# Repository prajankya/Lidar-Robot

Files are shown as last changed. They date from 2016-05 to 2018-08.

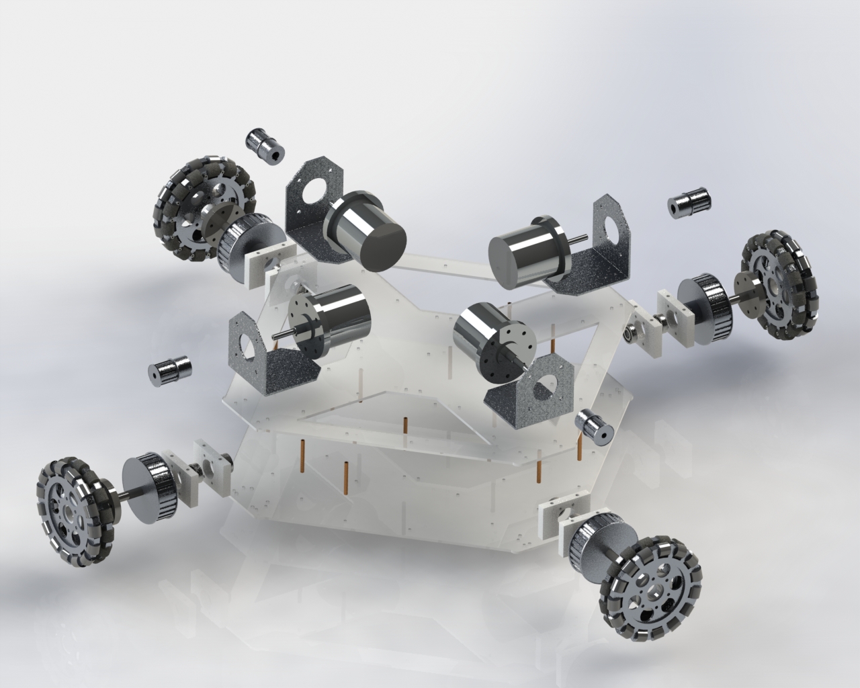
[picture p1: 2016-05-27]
Documentation/designs/r1.jpg

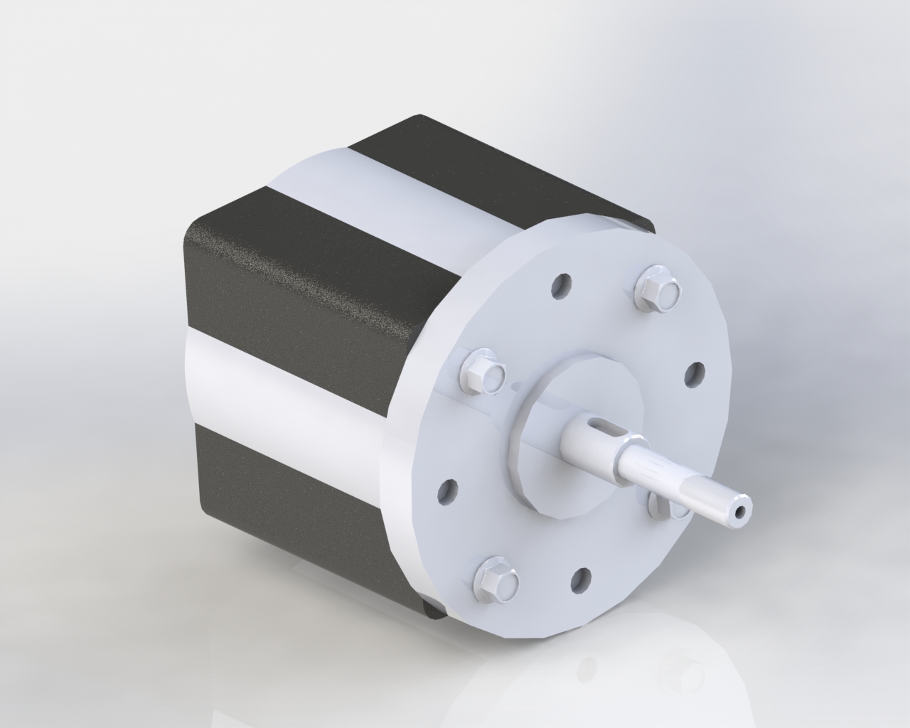
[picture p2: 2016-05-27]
Documentation/designs/r2.jpg

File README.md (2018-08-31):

  

## Unmanned Mapping Vehicle Using L.O.A.M. in Real-time
 L.O.A.M. - Lidar Odometry and Mapping in Real-time

This project is about an Unmanned Mobile Robot using L.O.A.M. (Lidar, Odometry And Mapping) in Real-time.

## Abstract
The robot uses a Laser distance sensor(Lidar) which gives distance to the first obstacle in its line-of-sight and the sensor. Making this sensor rotate gives us distance of all the obstacles from the sensor, which in fact is the map of the surrounding. This sensor, with other sensors like odometry and IMU(Inertial measurement Unit), mounted on a mobile moving base and complex algorithms driving the robot autonomously help make a to-scale map of the surrounding.

## Basic contruction
The Bot uses ROS(Robot Operating System) at its core running on a compact mobile CPU. It uses IMU(Inertial measurement Unit) for its orientation feedback. The base comprise of a square frame with four omni wheel on its corners driven by high torque BLDC motors. The Bot works on 24v DC and have internal power distribution and conversion unit. The bot first takes in the lidar input, and process that into a map fusing together with  odometry input and IMU input. The Odometry sensor is a “Castor Feedback sensor” which consist of two rotary encoders, one reading the angle or rotation, and other the length in that direction. This type of feedback can be universally used for any type of terrain robots with very good accuracy. This bot can be controlled from a remote computer, on which we can even see the 3D Model and see the model within the map in Real time. The GUI remote can be used to save the map or load the map in the system. Taking all the properties in consideration,  Lidar Robot with L.O.A.M. is a very robust platform with variety of robotics applications.

## How to Install
rosdep install --from-paths /opt/ros/jade --ignore-src

rosdep install --from-paths Lidar-Robot/src --ignore-src

6th sem, 2017 Batch  
Department of Automation and Robotics.  
B. V. Bhoomaraddi College of Engineering and Technology, Hubli  









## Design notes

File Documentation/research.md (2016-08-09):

#Papers which are to be refered

###Mapping with Synthetic 2D LIDAR in 3D Urban Environment
>Z. J. Chong, B. Qin, T. Bandyopadhyay, M. H. Ang, E. Frazzoli, and D. Rus, “Mapping with synthetic 2D LIDAR in 3D urban environment,” in 2013 IEEE/RSJ International Conference on Intelligent Robots and Systems, 2013, pp. 4715–4720.

In this paper, we report a fully automated detailed
mapping of a challenging urban environment using single
LIDAR. To improve scan matching, extended correlative scan
matcher is proposed. Also, a Monte Carlo loop closure detec-
tion is implemented to perform place recognition efficiently.
Automatic recovery of the pose graph map in the presence of
false place recognition is realized through a heuristic based
loop closure rejection. This mapping framework is evaluated
through experiments on the real world dataset obtained from
NUS campus environment.

###2D LIDAR Aided INS for vehicle positioning in urban environments
>S. Zhao and J. A. Farrell, “2D LIDAR Aided INS for vehicle positioning in urban environments,” in 2013 IEEE International Conference on Control Applications (CCA), 2013, pp. 376–381.

This paper presents a novel method to utilize 2D LIDAR for INS (Inertial Navigation System) aiding to improve 3D vehicle position estimation accuracy, especially when GNSS signals are shadowed. In the proposed framework, 2D LIDAR aiding is carried out without imposing any assumptions on the vehicle motion (e.g. we allow full six degree-of freedom motion). To achieve this, a closed-form formula is derived to predict the line measurement in the LIDAR's frame. This makes the feature association, residual formation and GUI display possible. With this formula, the Extended Kalman Filter (EKF) can be employed in a straightforward manner to fuse the LIDAR and IMU data to estimate the full state of the vehicle. Preliminary experimental results show the effectiveness of the LIDAR aiding in reducing the state estimation uncertainty along certain directions, when GNSS signals are shadowed.

#Literature Reviews to be refered

###A Review and Analysis of Literature on Autonomous Driving
>by Juan Rosenzweig, Michael Bartl

###An Evaluation of 2D SLAM Techniques Available in Robot Operating System
>J. M. Santos, D. Portugal, and R. P. Rocha, “An evaluation of 2D SLAM techniques available in robot operating system,” in 2013 IEEE International Symposium on Safety, Security, and Rescue Robotics (SSRR), 2013, pp. 1–6.

In this work, a study of several laser-based 2D
Simultaneous Localization and Mapping (SLAM) techniques
available in Robot Operating System (ROS) is conducted. All
the approaches have been evaluated and compared in 2D
simulations and real world experiments. In order to draw
conclusions on the performance of the tested techniques, the
experimental results were collected under the same conditions
and a generalized performance metric based on the k-nearest
neighbors concept was applied. Moreover, the CPU load of each
technique is examined.
This work provides insight on the weaknesses and strengths
of each solution. Such analysis is fundamental to decide which
solution to adopt according to the properties of the intended
final application.

###Navigation stack test: GMapping vs Hector Slam
>P. da alesi, “Geduino Foundation: Navigation stack test: GMapping vs Hector Slam.”

[http://geduino.blogspot.com/2015/04/navigation-stack-test-gmapping-vs.html](http://geduino.blogspot.com/2015/04/navigation-stack-test-gmapping-vs.html)

#Technology(papers) being used in the Project

###Robot Web Tools: Efficient Messaging for Cloud Robotics

Since its official introduction in 2012, the Robot
Web Tools project has grown tremendously as an open-
source community, enabling new levels of interoperability and
portability across heterogeneous robot systems, devices, and
front-end user interfaces. At the heart of Robot Web Tools
is the rosbridge protocol as a general means for messaging
ROS topics in a client-server paradigm suitable for wide
area networks, and human-robot interaction at a global scale
through modern web browsers. Building from rosbridge, this
paper describes our efforts with Robot Web Tools to advance: 1)
human-robot interaction through usable client and visualization
libraries for more efficient development of front-end human-
robot interfaces, and 2) cloud robotics through more efficient
methods of transporting high-bandwidth topics (e.g., kinematic
transforms, image streams, and point clouds). We further
discuss the significant impact of Robot Web Tools through
a diverse set of use cases that showcase the importance of a
generic messaging protocol and front-end development systems
for human-robot interaction.

##Some other related Papers to think upon
- Y. Lin, J. Hyyppä, and A. Kukko, “Stop-and-Go Mode: Sensor Manipulation as Essential as Sensor Development in Terrestrial Laser Scanning,” Sensors, vol. 13, no. 7, pp. 8140–8154, Jun. 2013.  

- I. Baldwin and P. Newman, “Road vehicle localization with 2D push-broom LIDAR and 3D priors,” in 2012 IEEE International Conference on Robotics and Automation (ICRA), 2012, pp. 2611–2617.  

- Y. Ma, H. Ju, and P. Cui, “Research on Localization and Mapping for Lunar Rover Based on RBPF-SLAM,” in International Conference on Intelligent Human-Machine Systems and Cybernetics, 2009. IHMSC ’09, 2009, vol. 2, pp. 306–311.  

- R. Zlot and M. Bosse, “Place Recognition Using Keypoint Similarities in 2D Lidar Maps,” Experimental Robotics, pp. 363–372, 2009.  

- F. Auat Cheein, G. Steiner, G. Perez Paina, and R. Carelli, “Optimized EIF-SLAM algorithm for precision agriculture mapping based on stems detection,” Computers and Electronics in Agriculture, vol. 78, no. 2, pp. 195–207, Sep. 2011.  

- J. R. Rosell, J. Llorens, R. Sanz, J. Arnó, M. Ribes-Dasi, J. Masip, A. Escolà, F. Camp, F. Solanelles, F. Gràcia, E. Gil, L. Val, S. Planas, and J. Palacín, “Obtaining the three-dimensional structure of tree orchards from remote 2D terrestrial LIDAR scanning,” Agricultural and Forest Meteorology, vol. 149, no. 9, pp. 1505–1515, Sep. 2009.  

- W. Maddern, G. Pascoe, and P. Newman, “Leveraging experience for large-scale LIDAR localisation in changing cities,” in 2015 IEEE International Conference on Robotics and Automation (ICRA), 2015, pp. 1684–1691.  

- M. Himstedt, J. Frost, S. Hellbach, H. J. Böhme, and E. Maehle, “Large scale place recognition in 2D LIDAR scans using Geometrical Landmark Relations,” in 2014 IEEE/RSJ International Conference on Intelligent Robots and Systems, 2014, pp. 5030–5035.  

- J. M. Santos, D. Portugal, and R. P. Rocha, “An evaluation of 2D SLAM techniques available in robot operating system,” in 2013 IEEE International Symposium on Safety, Security, and Rescue Robotics (SSRR), 2013, pp. 1–6.  

- S. Kohlbrecher, O. von Stryk, J. Meyer, and U. Klingauf, “A flexible and scalable SLAM system with full 3D motion estimation,” in 2011 IEEE International Symposium on Safety, Security, and Rescue Robotics, 2011, pp. 155–160.  

- M. Vázquez-Arellano, H. W. Griepentrog, D. Reiser, and D. S. Paraforos, “3-D Imaging Systems for Agricultural Applications—A Review,” Sensors (Basel), vol. 16, no. 5, Apr. 2016.  

- J. McCormack, J. Prine, B. Trowbridge, A. C. Rodriguez, and R. Integlia, “2D LIDAR as a distributed interaction tool for virtual and augmented reality video games,” in 2015 IEEE Games Entertainment Media Conference (GEM), 2015, pp. 1–5.  

- S. Zhao and J. A. Farrell, “2D LIDAR Aided INS for vehicle positioning in urban environments,” in 2013 IEEE International Conference on Control Applications (CCA), 2013, pp. 376–381.  

## Surveys to refer
- A. Elkady, T. Sobh, A. Elkady, and T. Sobh, “Robotics Middleware: A Comprehensive Literature Survey and Attribute-Based Bibliography, Robotics Middleware: A Comprehensive Literature Survey and Attribute-Based Bibliography,” Journal of Robotics, Journal of Robotics, vol. 2012, 2012, p. e959013, May 2012.  

- S. Thrun and others, “Robotic mapping: A survey,” in Exploring artificial intelligence in the new millennium, vol. 1, 2002, pp. 1–35.  

## Thesis to consider

- C. F. Ezequiel, “Real-Time Map Manipulation for Mobile Robot Navigation,” 2013.  

- “kelly_alonzo_1994_7.pdf.” .  

- A. S. Khusheef, “Investigation on the mobile robot navigation in an unknown environment,” 2013.

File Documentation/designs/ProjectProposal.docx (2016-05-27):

Minor Project

# Unmanned Mapping Vehicle Using L.O.A.M.[^1] in Real-time

Proposal, Technical Project

6th sem, 2017 Batch

Automation and Robotics Dept.

B. V. Bhoomaraddi College of Engineering and Technology, Hubli.

Team 9

Adarsh Belvatagi 2BV13AR002

Darshan Bafna 2BV13AR018

Manikanta Pujar 2BV13AR031

Prajankya Sonar 2BV13AR043

Table of Contents

1. Introduction
  1.1. Problem Statement
  1.2. Background
2. Proposed Technical Approach
  2.1. Features (Functions)
  2.2. Architectural Design
  2.3. Hardware:
  2.4. Software:
3. Expected Result
  3.1. Measure of Success

Introduction

## 1.1. Problem Statement

Design an Autonomous IOT based 2D mapping device.

## 1.2. Background

Lot of manpower and resources are invested in surveying road,tunnels, sewages and all other areas which need mapping. To optimise this process we came up with a plan to make a device which will ease this process. Semi or fully autonomous.

Proposed Technical Approach

## 2.1. Features (Functions)

1.Given an Absolute point to the vehicle it should reach that point avoiding all the obstacles

2.Localizing itself automatically in an unknown place when given the map of that area

3.It can report back its state to a known host(through wifi or internet or bluetooth or any other media)

## 2.2. Architectural Design

### Hardware:

- RPlidar
- IMU
- GPS
- UltraSonic
- Base with 4 Omni wheels
- IoT Connectivity(Wifi, Bluetooth, etc)

### Software:

- Robot Operating System
- Rviz
- Gazebo

# 3. Expected Result

## 3.1. Measure of Success

(how are we going to verify that the project is successful)

The project will be successful when the map made by our device is verified by physical measurements .

[^1] L.O.A.M. - Lidar Odometry and Mapping in Real-time

Automation and Robotics, B. V. Bhoomaraddi College of Engineering and Technology,Hubli.

Last Updated On : 27-JAN-2016

Project Proposal

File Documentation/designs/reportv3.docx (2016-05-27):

Minor Project

# Unmanned Mapping Vehicle Using L.O.A.M.[^1] in Real-time

Technical Report

6th sem, 2017 Batch

Automation and Robotics Dept.

B. V. Bhoomaraddi College of Engineering and Technology, Hubli.

Team 9

Adarsh Belvatagi 2BV13AR002

Darshan Bafna 2BV13AR018

Manikanta Pujar 2BV13AR031

Prajankya Sonar 2BV13AR043

# Table of Contents

1. Requirement list
2. Functional Analysis
3. Performance specification
  3.1. Rplidar
  3.2. IMU [GY80]
    3.2.1. L3G4200D: Gyroscope
    3.2.2. ADXL345- Digital accelerometer
    3.2.3. HMC5883L 3 axis Digital compass
  3.3. Intel NUC DN2820
  3.4. Power supply
  3.5. Screw & Bolt
  3.6. Material for base
4. Morphological chart
5. Detailed design and Production drawings
  5.1. Mechanical
  5.2. Electronics
6. Bill of materials & Component Procurement
  6.1. Electronics
  6.2. Mechanical
7. Hardware / Software architecture
8. Model In Iterations & Improvement Cycle
9. Component Testing
10. Characterization
11. Software prototyping
12. Components Manufacturing
  12.1. Mechanical components manufacturing
  12.2. Electronics components manufacturing

# Abstract:

This project is about an Unmanned Mapping Vehicle Using L.O.A.M. in Real-time that is achieved by using ROS( Robotic Operating System) which will map any indoor environment, RPlidar is an sensor that will help us to map the environment, for navigation of the bot IMU(Inertial measurement unit ) is used. RPlidar and IMU are connected to Arduino and inturn it is connected to NUC mini computer which is on the bot, all the commands are sent to master in NUC from the maincontroller.

# Introduction:

Mapping, localization, and path-planning are three fundamental problems of robot. Robot needs a map to perform actions like path-planning. When positioning system is not available, the map is also used for localization. Therefore here we use an RPLIDAR to help us map the indoor environment with the help of Robotic Operating System in 2D.

# 1. Requirement list

  1.1. Autonomous 3D mapping device
  1.2. Bot should be compact
  1.3. Generate 3D map of the environment and save it
  1.4. It should avoid obstacle
  1.5. It should be independent
  1.6. It should locate itself when left in an unknown terrain`
  1.7. Bot should be light weight
  1.8. Should have emergency stop button
  1.9. Battery backup should be good
  1.10. The bot could be manually overridden with the help of an Graphical User Interface

# 2. Functional Analysis

  2.1. 3D mapping
    2.1.1. RP LIDAR(sensor)
  2.2. Autonomous
    2.2.1. Locomotion
    2.2.2. Power supply
    2.2.3. Obstacle detection
  2.3. Storage
    2.3.1. Memory to save the data of the 3D map
  2.4. Manual control
    2.4.1. Use of an remote joystick to manually control the bot using an GUI.

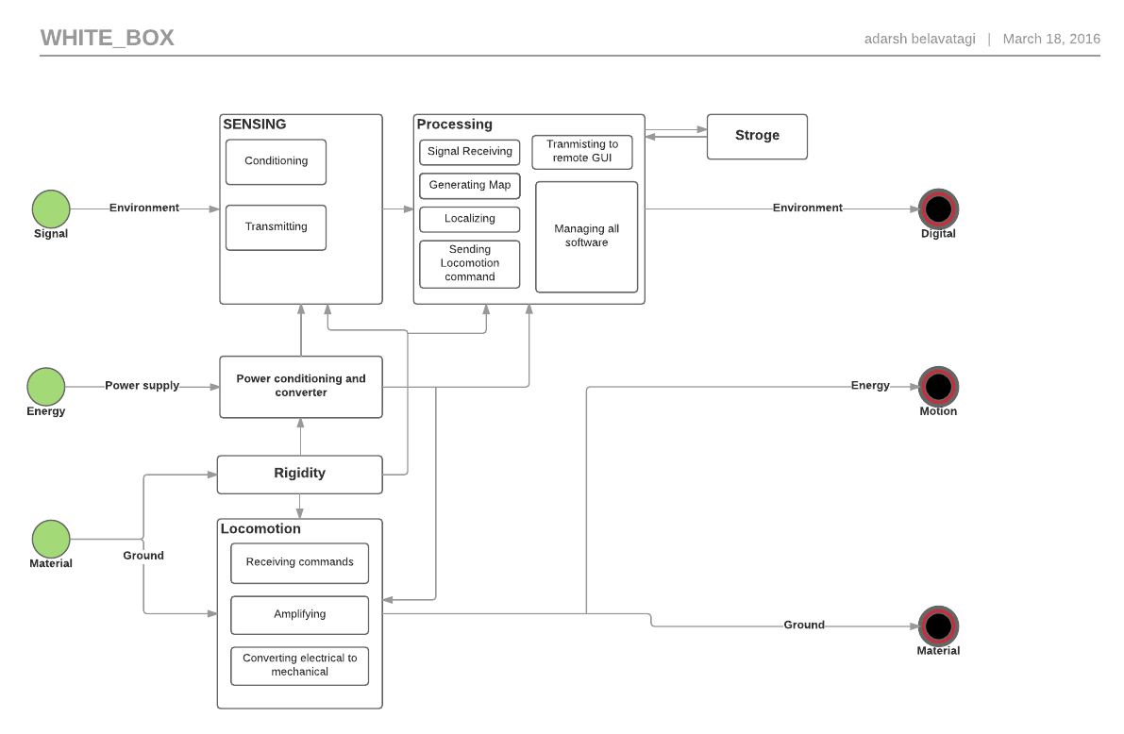
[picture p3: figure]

# 3. Performance specification

## 3.1. Rplidar

    3.1.1. Range: 0.2 m(min)\
    3.1.2. 6.0 m(max)
    3.1.3. Angular range : 0-360 Degree
    3.1.4. Distance Resolution: 60mm
    3.1.5. Angular Resolution: 1 Degree
    3.1.6. Sample Frequency :>=2000 Hz
    3.1.7. Scan rate : 5.5 Hz
    3.1.8. i/p voltage : 6V
    3.1.9. o/p voltage : 6V
    3.1.10. Weight: 170 gm

## 3.2. IMU [GY80]

    3.2.1. L3G4200D: Gyroscope
      3.2.1.1. Measurement range:± 500 dps
      3.2.1.2. Sensitivity :17.5 mdps/digital
      3.2.1.3. Digital zero rate level: ±15dps
      3.2.1.4. Zero rate level charging v/s temp:±0.04dps
      3.2.1.5. Non linearity:0.2 of measurement range
      3.2.1.6. Rate noise density: 0.03 dps/sqrt HZ for 150 HZ
      3.2.1.7. Operating temp: -40 to 80 c\
    3.2.2. ADXL345- Digital accelerometer
      3.2.2.1. Measurement range: ± 2 ±4 ±6 ±8 ±16 g
      3.2.2.2. Output resolution: 12 bits for ±8 g range
      3.2.2.3. Noise (x,y axis): 0.75 LSB rms Z direction 1.1 ILS me
      3.2.2.4. Power supply: min 140mA 5V
      3.2.2.5. Operating temp: -40 to 85 ∘C
    3.2.3. HMC5883L 3 axis Digital compass
      3.2.3.1. Supply voltage: 2.16 to 3.6V
      3.2.3.2. Field range: -8 to +8 gauss
      3.2.3.3. Magnetic dynamic range: ±1- ±8 gauss
      3.2.3.4. Sensitivity: 220 to 1370 ISB /gauss
      3.2.3.5. Operating temp: -40 to 85 ∘C

## 1.1. Intel NUC DN2820

    3.2.4. Processor: Intel Celeron Processor N2820
    3.2.5. Memory: 8gb max
    3.2.6. Graphics: Intel HD graphics up to 756 MHz
    3.2.7. Peripheral Connectivity
      3.2.7.1. 1 * USB 3.0 port on the front panel
      3.2.7.2. 2 * USB 2.0 port on the back panel
      3.2.7.3. Front panel 1R sensor
    3.2.8. Storage: Internal for 2.5 inch HDD or SSD
    3.2.9. Dimensions: 116.6 mm *112mm*515mm
    3.2.10. Power adapter: 12V 36W wall mount AC

## 3.3. Power supply

    3.3.1. Lithium polymer - (11.2V 5.5A)
    3.3.2. UBEC - Input 24V Output 12V
  3.4. Screw & Bolt
    3.4.1. Size M4
  3.5. Material for base
    3.5.1. Acrylic

# 4. Morphological chart

Sl.no | FUNCTION | Alternative1 | Alternative2 | Alternative 3
1 | Sensing
1.1 | obstacle | IR | LIDAR | Proximity
1.2 | Position/Orientation | Gyro | Magnetic | IMU
1.3 | Surrounding | LIDAR | Kinect | Image processing
2 | Processing
2.1 | Signal Receiving | ATMEL | Intel NUC | RASBERRY
2.2 | Generating Maps | ROS | Hector_mapping
2.3 | Localizing | AMCL | ROS_hector
2.4 | Localizing commands | Microcontroller (arduino ,PLC) | Microprocessor | FPGA
2.5 | Managing all programs | ROS | Custom programming | Player_Stage
2.6 | Storage | Hard Drives | Google Drive(cloud) | Intel NUC
2.7 | Transmitting to Remote GUI | RF | wifi | Optical link
2.8 | Power conditioning | Transformer filter circuit | Battery Eliminator circuit | Linear regulator circuit
3 | Locomotion
3.1 | Receiving commands | Microcontroller (arduino,PIC) | Microprocessor | FPGA
3.2 | Amplifying | Motor driver | H-bridge | Relay operated
3.3 | Converting electrical to Mechanical | solenoid | motor
4 | Rigidity
4.1 | Between motor and base | L clamp | C CLAMP | Screw and nuts
4.2 | Between two acrylic sheet | C clamp | Screws and nuts | Studs and screws

WHY Rplidar?

| Hokuyo URG-04LX Scanning Laser Rangefinder | Parallax 15-122cm Laser Rangefinder | Hokuyo UTM-30LX-EW Scanning Laser Rangefinder | Loke 0.2 to 30m Industrial Laser Distance Meter (10Hz) | Loke 0.2 to 35m Industrial Laser Distance Meter (50Hz) | Hokuyo UXM-30LN-PW Scanning Laser Rangefinder (http://www.robotshop.com/en/hokuyo-uxm-30ln-pw-scanning-laser-rangefinder.html) | Hokuyo UST-10LX Scanning Laser Rangefinder (http://www.robotshop.com/en/hokuyo-ust-10lx-scanning-laser-rangefinder.html) | RPLIDAR 360° Laser Scanner (http://www.robotshop.com/en/rplidar-360-laser-scanner.html) | LeddarTech LeddarOne Optical Rangefinder (RS-485) (http://www.robotshop.com/en/leddartech-leddarone-optical-rangefinder-rs-485.html)
| RB-Hok-01 | RB-Plx-257 | RB-Hok-16 | RB-Hok-11 | RB-Hok-09 | RB-Hok-14 | RB-Hok-24 | RB-Rpk-01
Serial (UART) Pins | 1 | 1 | 0 | 0 | 0 | 0 | 0 | 1 | 0
USB | 1 | 0 | 1 | 0 | 0 | 1 | 0 | 1 | 0
Nominal Current [A] | 0.5 | | 0.7 | 0.0042 | 0.0042 | 0.3 | | 130
Nominal Voltage [V] | 5 | 5 | 12 | | | 24 | | 5 | 5
Voltage (Min) [V] | | | 0 | 10 | 10 | | 0.15 | 3.6 | 5
Weight | 160 g | | 370 g | 500 | 4000 g | 800 g | 130 g | 200 g
Accuracy [mm] | 60mm à 1m : ±10mm, 1m à 5m : 1% de la distance | <5%, average 3% | 0.1 to 10m:±30mm, 10 to 30m:±50mm*1 | ±2 mm à ± 5 mm | Environ ±2mm | 0.1 to 10m : ±50mm, 10 to 30m : ± 100mm | +/- 40mm | <0.5mm (1% of the distance) | 50
Angular Resolution [°] | 0.36 | | 0.25 | | | 0.25 | 0.25 | 1
Distance Min | 20 mm | 0 mm | 30000 mm | 200 mm | 200 mm | 100 mm | 20 mm | 200 mm | 0 mm
Angle [°] | 240 | | 270 | | | 190 | 270 | 360
Scan Time | 100 | | 25 | | | 50 | 25 | 0.18
Voltage (Max) [V] | | | | 30 | 30 | | | 9 | 5
Distance Max | 4000 mm | 2400 mm | 60000 mm | 150000 mm | 150000 mm | 30000 mm | 10000 mm | 6000 mm | 20000 mm

From the above comparison of sensors ,We can Notice that Rplidar as good characteristics and its cost is also less comparative to other sensors..

# 1.Sensing

### 1.1 & 1.3 Obstacle detection and surrounding sensing

Rp lidar 360°- is preferred than IR and PROXIMITY sensor because A laser scanner development kit with omnidirectional laser scan,it works on the principle of laser triangular whose speed is very high, it is the ideal sensor for robot localization, mapping & obstacle detection and safety ,it has the range of 6 meters ,1 degree angular resolution,5v power supply.

### 1.2 Position and orientation- IMU

- IMU is used because it consist of 4 sensors i.e ADXL345 digital accelerometer ,HMC5883L digital compass, L3G4200D gyroscope and BMP085 digital barometer which gives the sensor 10DOF , there are built in regulator and logic converter to support 3.3V/5.0V microcontrollers, 12C digital interface,The sensor is very compact too.

# 2.Processing

### 2.1 Signal receiving - Intel NUC

Intel NUC is a compact mini computer with full-size computing power, lots of I/O ports ,IR receiver and with a smaller footprint than a wireless modem, the Intel NUC with the 4th generation Intel Core i5 processor It also includes Intel Rapid Start Technology, ensuring you are quickly up and running, and Intel Smart Connect Technology to keep you up to date at all times.

### 2.2 Generating maps: ROS

Robotic operating system has an 3D visualizer tool called as RVIZ which helps us to generate the map with utmost accuracy and helps us to visualize the map in real time .

### 2.3 Localizing: ROS_HECTOR

Hector_mapping is a SLAM approach that can be used without odometry as well as on platforms that exhibit roll/pitch motion (of the sensor, the platform or both). It leverages the high update rate of modern LIDAR systems like the Hokuyo UTM-30LX and provides 2D pose estimates at scan rate of the sensors (40Hz for the UTM-30LX).

### 2.4 Localizing commands: Micro controller

Commands to the bot are given by the microcontroller

### 2.5 Managing all programs:ROS

ROS is an open-source, meta-operating system for your robot. It provides the services you would expect from an operating system, including hardware abstraction, low-level device control, implementation of commonly-used functionality, message-passing between processes, and package management. It also provides tools and libraries for obtaining, building, writing, and running code across multiple computers. ROS is similar in some respects to 'robot frameworks’

### 2.6 Storage: Intel NUC

Since we are using mini computer we have an storage space of 1.5 to 2 TB of data can be stored which is more than enough to store the maps and navigation data.

### 2.7 Transmitting to Remote GUI: Wifi

Since our mini computer has the facility of wireless communication we take the advantage of this facility and reduce the complication of keeping an receiver and transmitter.

### 2.8 Power conditioning:UBEC

It is an universal battery eliminator circuit is an electronic circuit (https://en.wikipedia.org/wiki/Electronic_circuit) designed to deliver electrical power (https://en.wikipedia.org/wiki/Electric_power) to other circuitry without the need for multiple batteries (https://en.wikipedia.org/wiki/Battery_(electricity)). Historically the expression was sometimes used to describe devices used to power battery-driven equipment from mains electricity. This is still the case in many products offered in retail electronic supply stores.

## 3.Locomotion

### 3.1 Receiving commands:Microcontroller (arduino,PLC):

Commands are sent to the bot via arduino software through ROS and microcontroller receives the commands and induces locomotion.

### 3.2 Amplyifying : Motor driver

Signals from the microcontroller are sent to motor via motor driver where the signals gets amplified

### 3.3 Electrical to mechanical:Motor

Motor converts the electrical signal received from the driver and converts them into mechanical energy for the locomotion.

## 4.Rigidity

### 4.1 Between motor and base of the bot: C clamp

As the motor is placed between two acrylic sheet(base) so C-clamp is used to fix the motor to the bot base for stability

### 4.2 Between 2 acrylic sheet: Studs and screws

To fix the two acrylic sheets we use Studs and and screws of size M4

# 5. Detailed design and Production drawings

## 5.1. Mechanical

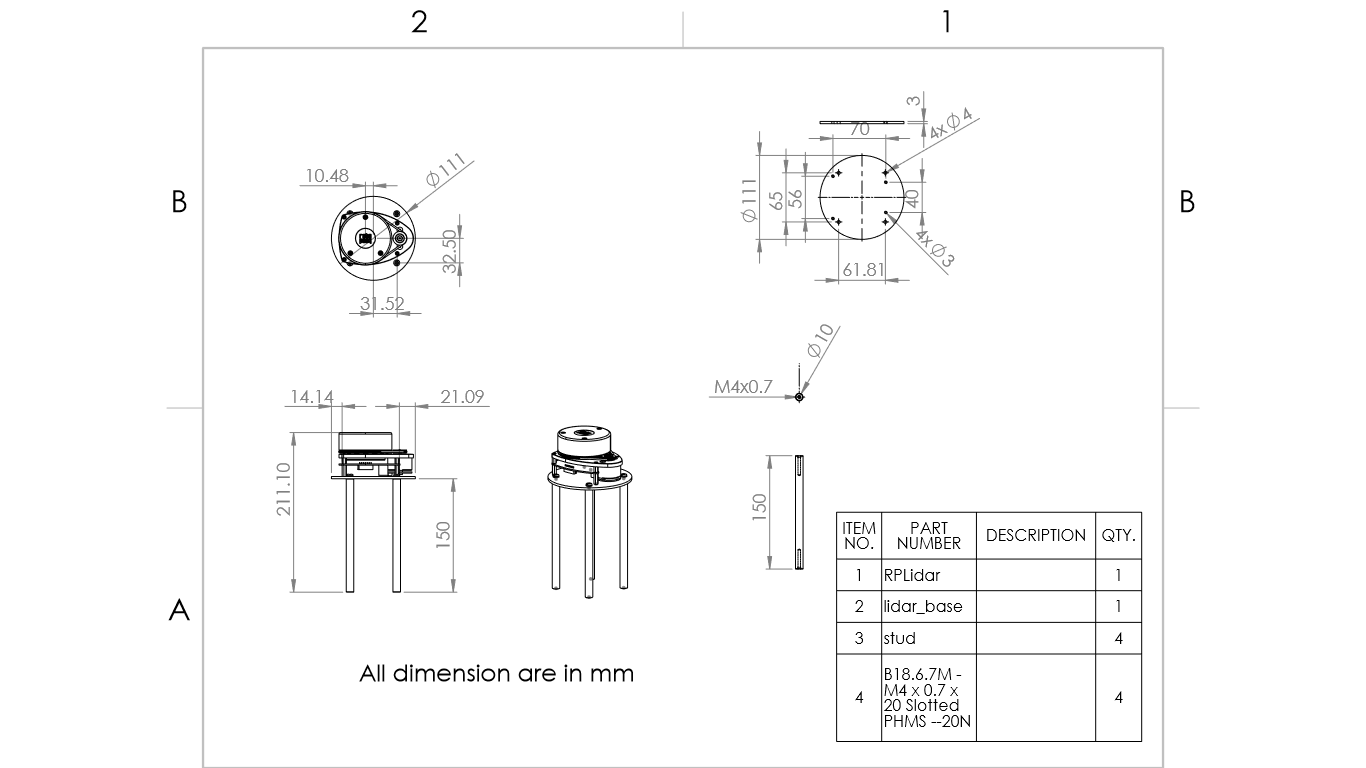
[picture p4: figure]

## 5.2. Electronics

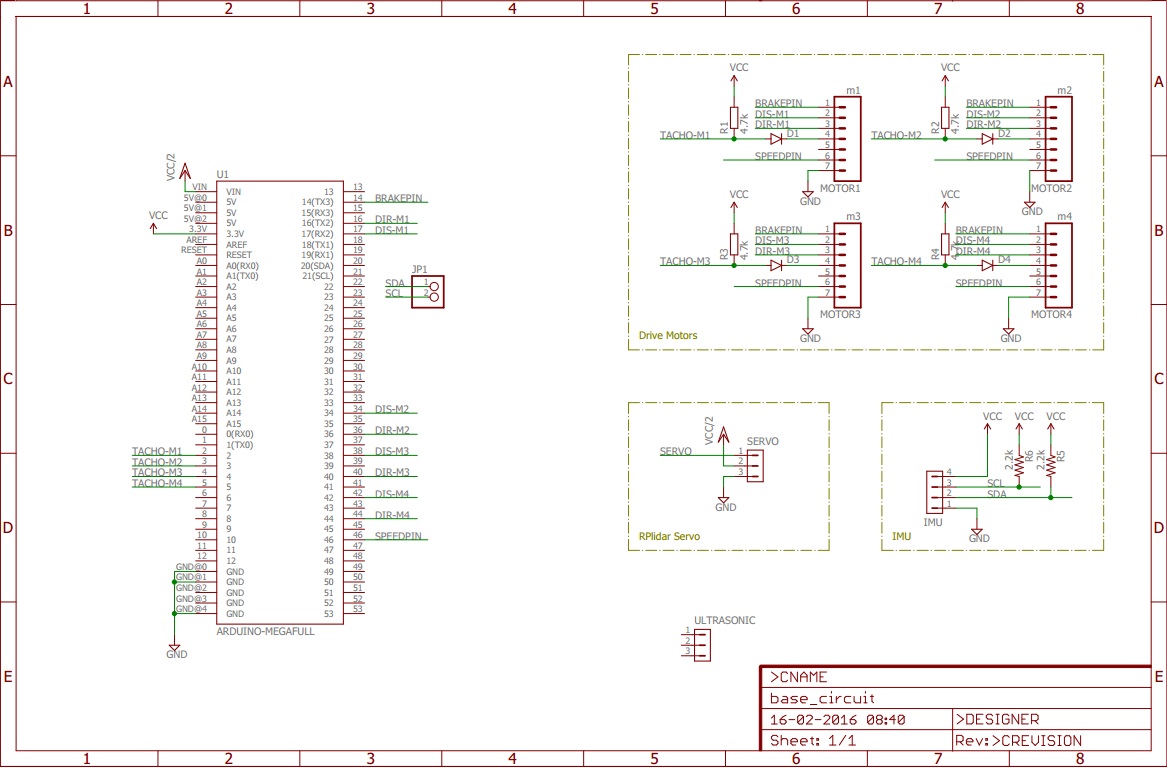
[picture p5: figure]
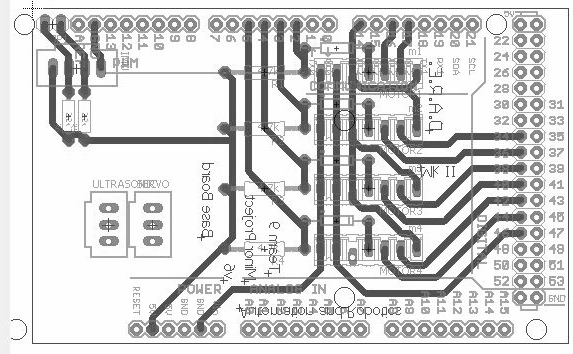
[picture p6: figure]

# 6. Bill of materials & Component Procurement

## 6.1. Electronics

SL.NO | COMPONENT | QUANTITY | VENDOR | Price
1 | RPlidar | 1 | Tennettech.com | 37000₹
2 | IMU 10dof | 1 | Probots.co.in | 1000₹
3 | NUC mini Pc | 1 | Dept. of Automation & Robotics | 10000₹
4 | Resistors 330 ohm | 2 | New Gokhale Electronics | 4₹
5 | Motor | 4 | Robu.in | 20000₹
6 | Motor Driver | 4 | Robu.in | 20000₹
7 | Resistors 2.2k ohm | 4 | New Gokhale Electronics | 4₹
8 | 8pin connector male | 4 | New Gokhale Electronics | 60₹
9 | 8pin connector female | 4 | New Gokhale Electronics | 60₹
10 | PCB | 1 | New Gokhale Electronics | 30₹
11 | Power supply 22.2V | 2 | robomart.com | 13800₹
12 | UBEC | 1 | robomart.com | 1000₹
13 | Screw Terminal | 2 | micro electricals | 20₹

## 6.2. Mechanical

SL.NO | COMPONENT | QUANTITY | Material VENDOR | Price
1 | OMNI wheels | 4 | Robu.in | 36000₹
2 | C-clamp | 4 | Fabricated | 285₹
3 | Studs 2 1/2 | 35 | Asian hardware | 169₹
4 | Base board | 2 | Fabricated | 1480₹
5 | Nuts(M4) and Bolts(M4) | 78 | Asian hardware | 565₹
6 | motor shaft | 4 | rupa metals | 245₹
7 | Side link | 1 | Fabricated | 50₹
8 | Feedback wheel | 1 | Fabricated | 60₹
9 | Feedback base | 1 | Fabricated | 60₹
10 | Hight plate | 1 | Fabricated | 60₹

# 7. Hardware / Software architecture

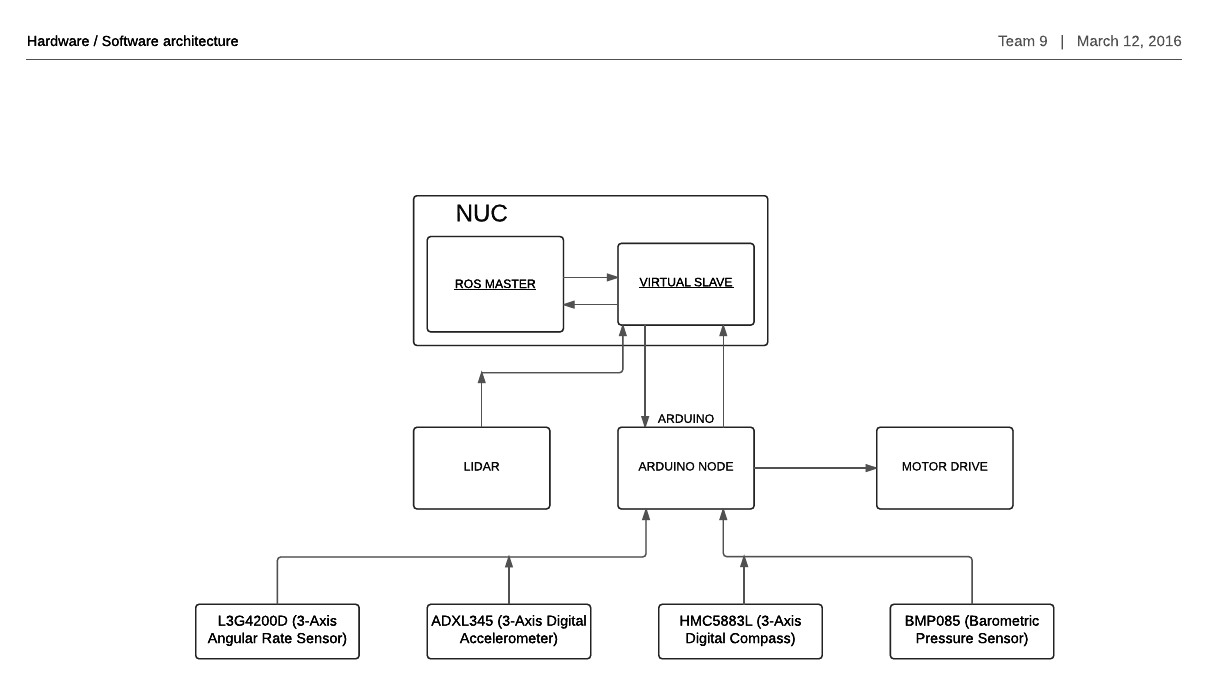
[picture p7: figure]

Hardware consists of NUC mini computer which has the ROS master which communicates with a Virtual slave within it, RPlidar sends the real time information to the virtual slave i.e in NUC which intern communicates with the master and makes the map of the surrounding along with this we have have arduino communicating with the slave through a Node that is created by ROS and controls the motor drivers,we have IMU i.e inertial measurement unit which consist 4 sensors Angular rate sensor,Digital accelerometer, Digital compass and Barometer all this sensors communicate in real time with ROS via arduino node in arduino and virtual slave in NUC.

# 8. Model In Iterations & Improvement Cycle

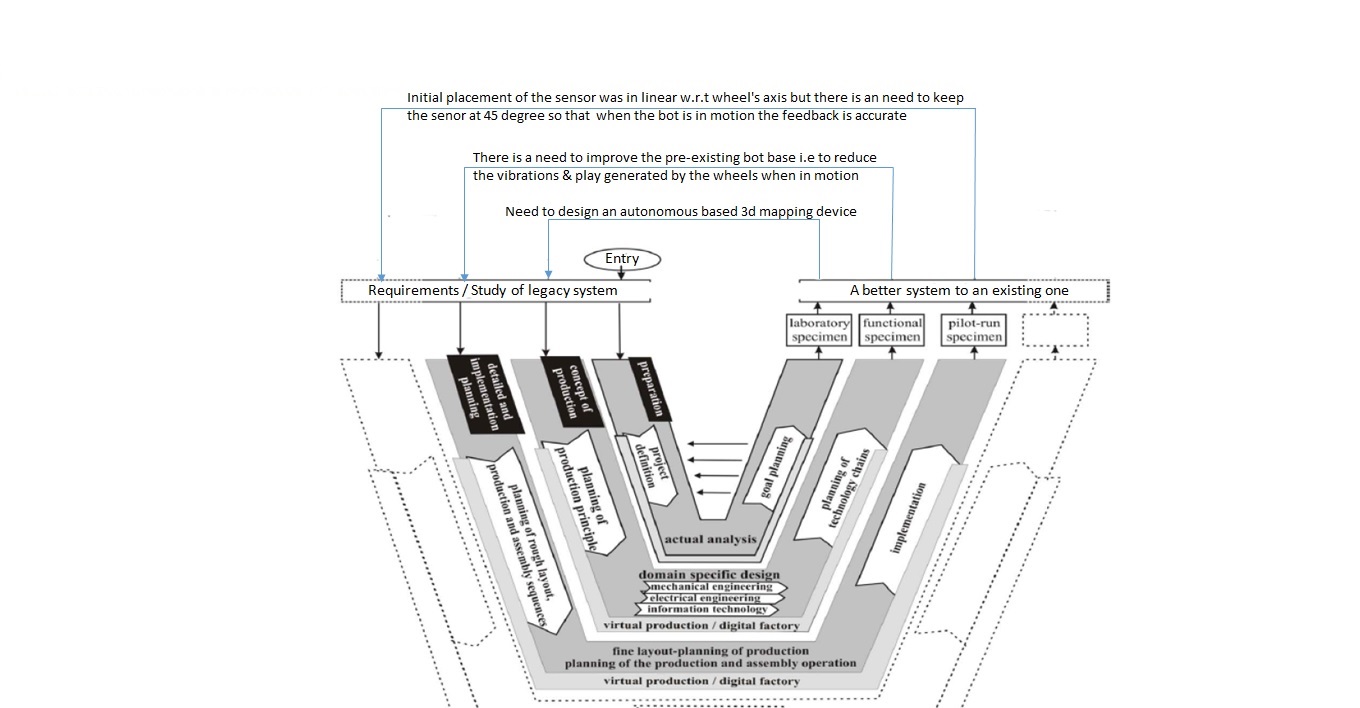
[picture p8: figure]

This is an iterative V-model where we have shown how our project was carried out from the start .

- Preparation for the project ,we defined the project definition followed by the project goal planning
- According to the plan we have to design an autonomous 2d mapping device
- In next iteration we started to modify the design of the existing according to our requirements
- We did the analysis our bot in software as well as the physical existing one in terms of mechanical stability ,electrical side and programming part
- After the analysis we verified the results with our requirements, there was a need in the improvement of the bot i.e ,maintain the stability and control the vibrance , make a feedback system for the odometry fix RP lidar on the bot.
- Now we did the detailed

# 9. Component testing

## 9.1. Electronics

    9.1.1. IMU “Tested by interfacing with arduino: example programs were used to check the working of each of the 4 sensors, and all the values were found to be same as per the commands given ”
    9.1.2. LIDAR “Tested by interfacing with ROS: lidar was interfaced to Robotic Operating system and RViz tool was used to check the map created by the Lidar after the lidar was made to scan the room, it was found that the range if the Lidar is 6m as mentioned in the specs of the sensor and error in the measurement was negligible i.e 0.02cm ”
    9.1.3. Motor Driver “ Tested by interfacing with arduino: Signals from arduino were given to the driver and it was found that the motors were working as the commands were given to the driver by the software ”
    9.1.4. Arduino “ Tested by Uploading & Running Blink LED program :Working of the arduino board ”
    9.1.5. Motors “Tested by connecting with battery: all four motors were connected to LIPO 22.3V battery and were tested ”
    9.1.6. PCB board “Probe Test: board was designed in Eagle software and then board was fabricated by the method of etching,then with the help of probes connectivity and continuity check was done ”
    9.1.7. Power supply 22.2V “Tested Using Multimeter: Tested continuosly the battery ”
    9.1.8. UBEC “ Tested Using Multimeter ”

## 9.2. Mechanical

    9.2.1. OMNI wheels “Tested by Creating Solidworks model and mounting to shaft ”
    9.2.3. C-clamp “ Tested by Creating Solidworks model and mounting to motor”
    9.2.5. Studs “Tested by Creating Solidworks model and mounting between the base boards ”
    9.2.6. Baseboard “ Tested by Creating Solidworks model”

# 10. Characterization

SL.NO | Component | Expected values | Measured values
1 | LIDAR | 6M,0°-360°rotation | 6M,0°-360°rotation
2 | Gyroscope (L3G4200D) | ±2000 dps | reasonable
3 | Digital accelerometer (ADXL345) | At± 2g sensitivity=256 LSB/g | ±0.005 g noise at stationary position
4 | Digital compass (HMC5883L) | Accuracy 2deg | 1~2 deg drift

# 11. Software prototyping

The RPlidar is connected to a mobile computer,which give a information about surrounding.In the mini-computer the robot oprating sysytem is installed,This help to set mini computer as Master node and help in creating slave nodes .there is a virtual slave in the mini-computer which is receiving and prosessing the input from the RPlidar .A hardware slave node (i.e.,Arduino) connected to mini-computer which give motor feedback and IMU input to mini computer.The RPlidar and IMU work together to collect the information about surrounding ,the collected information is processed and 2D map of Environment is created in the GUI,Based on the 2D map the bot avoid the obstacles and move.

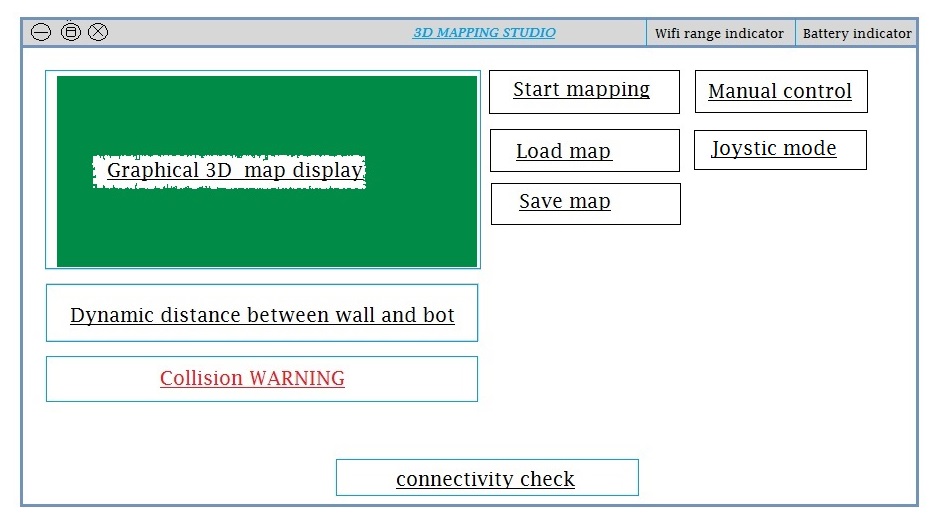
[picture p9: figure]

### Graphical user interface prototype (Front end)

# 12. Components Manufacturing

## 12.1. Mechanical components manufacturing

SL.NO | components | material | manufacturing process
1 | C-clamp | aluminium | bending & machining
2 | Pulley Shaft | aluminium | machining(lathe machine)
3 | Baseboard | acrylic | machining(cnc router)
4 | Studs 150mm | aluminium | machining(lathe machine)
5 | LIDAR base | acrylic | machining(cnc router)

## 12.2. Electronics components manufacturing

SL.NO | components | manufacturing process
1 | Baseboard PCB | etching

# 1.Cost of the components

List of the component | Cost of the component
RPlidar | 37000/-
wheels | 36000/-
Motors and Drivers | 40000/-
Timer pulley | 16000/-
Stud | 10000/-
NUC | 10000/-
IMU | 1000/-
UBEC | 1000/-
Batteries | 8400/-
Wires | 500/-
Other electronics | 1000/-
GPU | 42000/-
Total : | 203000/-

[^1] L.O.A.M. - Lidar Odometry and Mapping in Real-time

Automation and Robotics, B. V. Bhoomaraddi College of Engineering and Technology,Hubli.

Review report

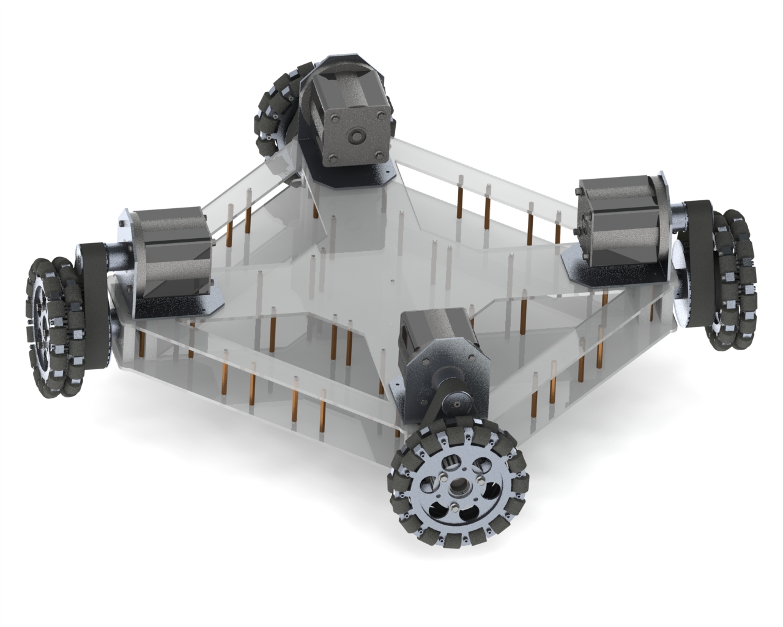
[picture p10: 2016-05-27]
Documentation/designs/r3.jpg

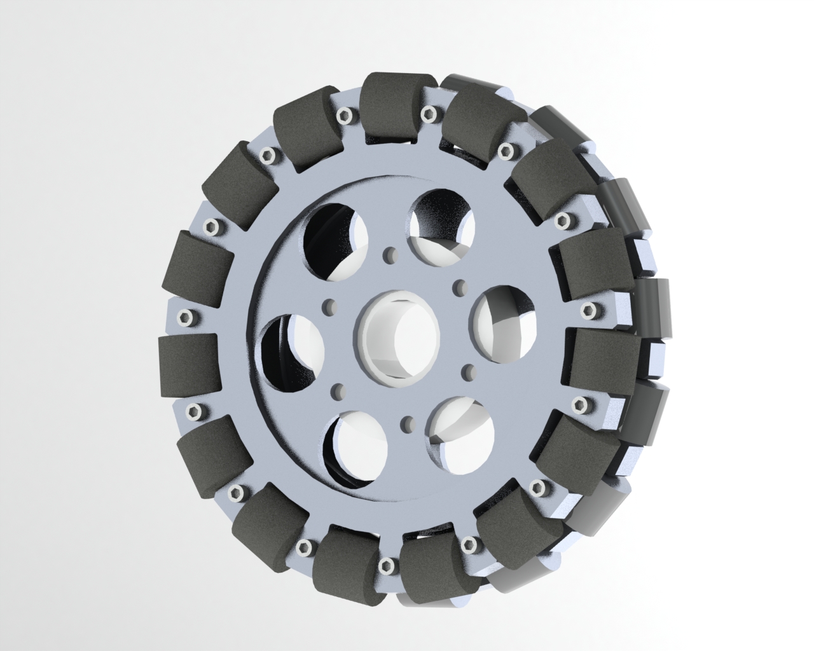
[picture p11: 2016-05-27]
Documentation/designs/r4.jpg

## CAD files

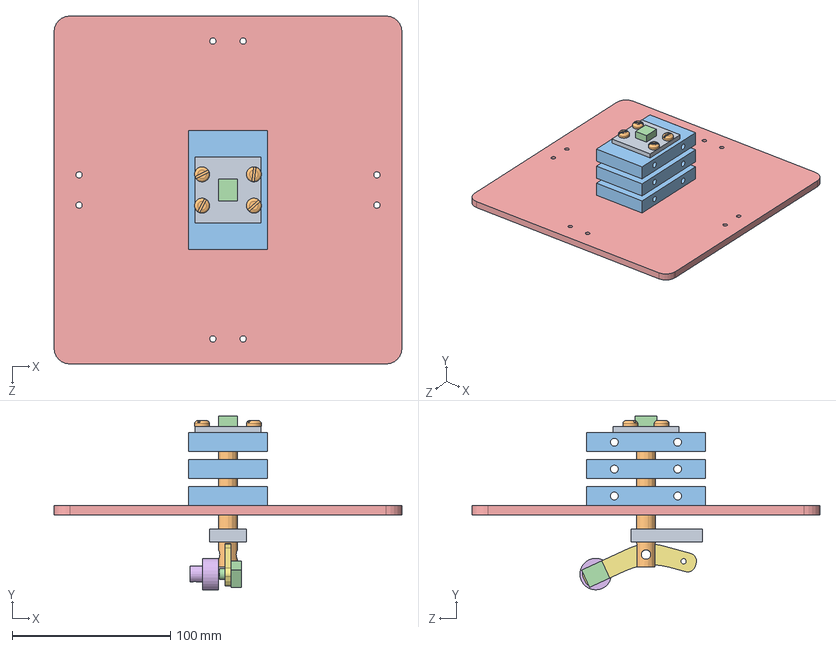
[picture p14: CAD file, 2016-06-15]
CAD/solidworks_model/MAIN_FEEDBACK.SLDASM
220.0 x 109.9 x 220.0 mm
Feedback_base
caster_shaft
Lower Clamp x 3
encoder x 2
cutbase
wheel
sidelink
radial ball bearing_68_skf x 3
top_ecoder_holder
pan slot head_am x 4

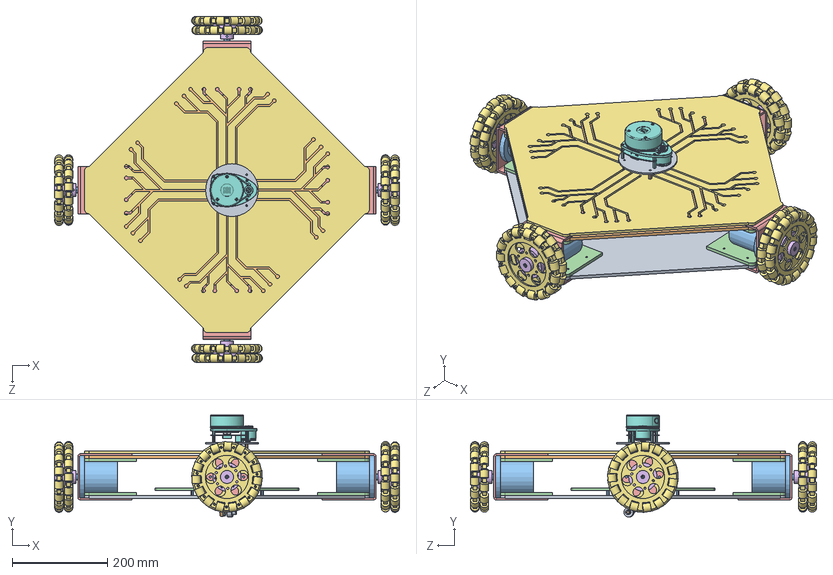
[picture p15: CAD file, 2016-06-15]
CAD/solidworks_model/final_base.SLDASM
726.0 x 214.5 x 728.5 mm
Base Plate1
Base Plate
Motor x 4
base_height x 8
l_clamp x 4
shaft x 4
Omni Wheel x 4
sidelink
wheel
encoder x 2
stud15mm x 8
cutbase
caster_shaft
Lower Clamp x 3
circit1
Lidar
lidar_base
15mm__studSLDPRT x 4
Feedback_base
feedback band

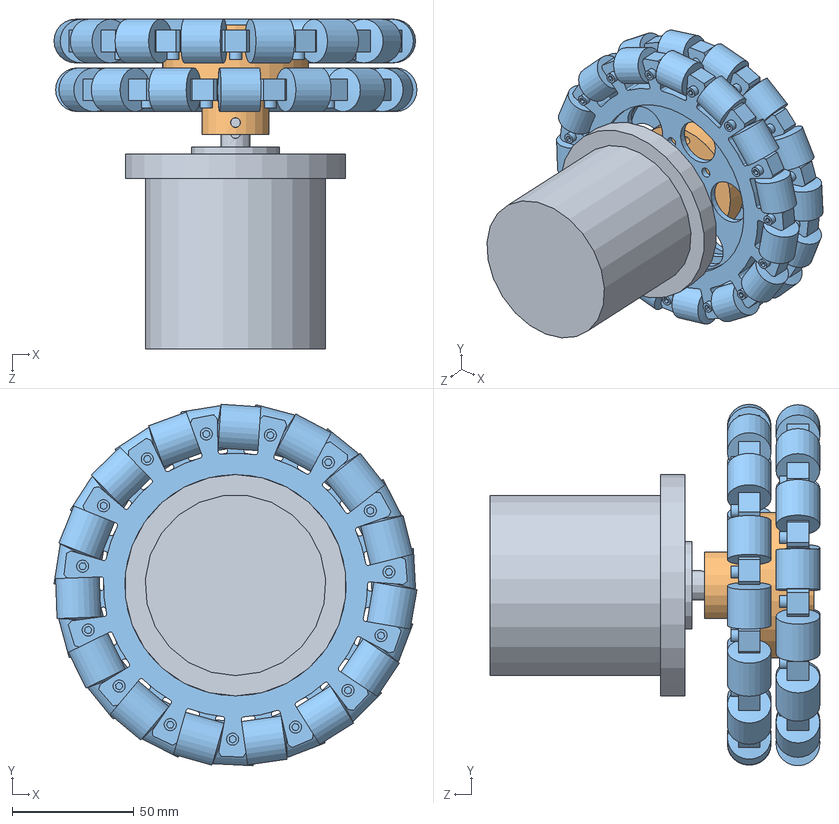
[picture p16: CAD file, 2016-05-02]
CAD/solidworks_model/shaft_motor.SLDASM
149.2 x 148.6 x 135.5 mm
Motor
shaft
Omni Wheel

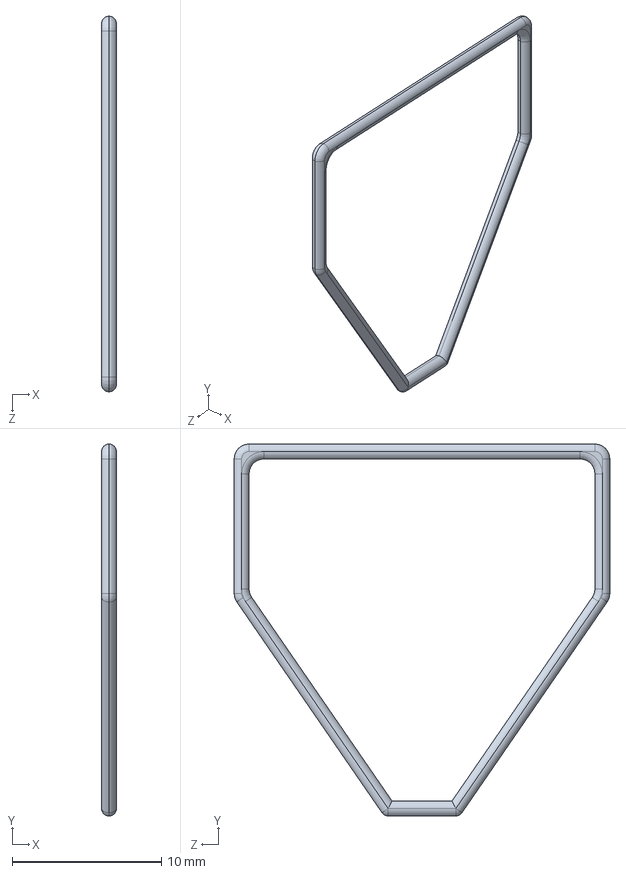
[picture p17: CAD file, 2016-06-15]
CAD/solidworks_model/feedback band.SLDPRT
1.00 x 24.9 x 25.1 mm

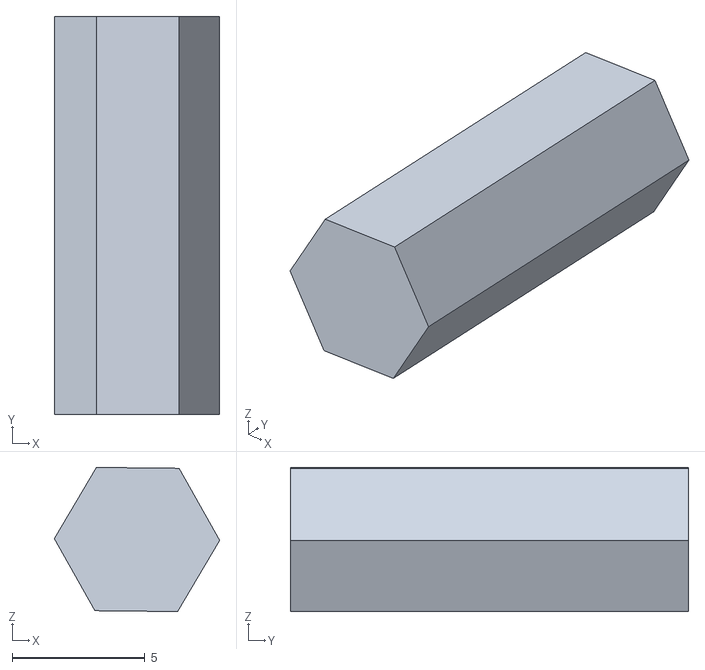
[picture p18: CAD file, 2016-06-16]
src/lidar_robot/models/stud.stl
6.24 x 15.0 x 5.43

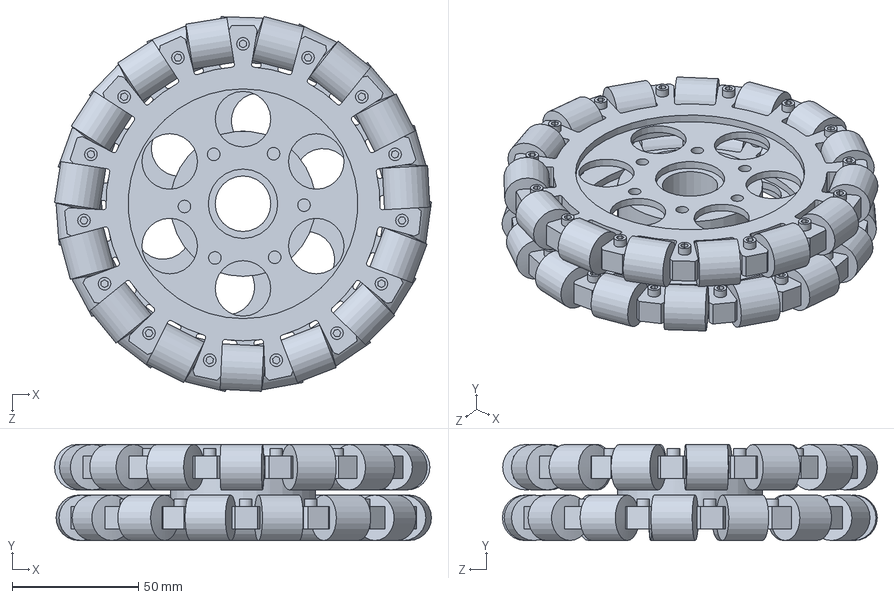
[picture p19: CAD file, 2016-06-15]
CAD/solidworks_model/Omni Wheel.SLDPRT
149.2 x 38.0 x 148.5 mm

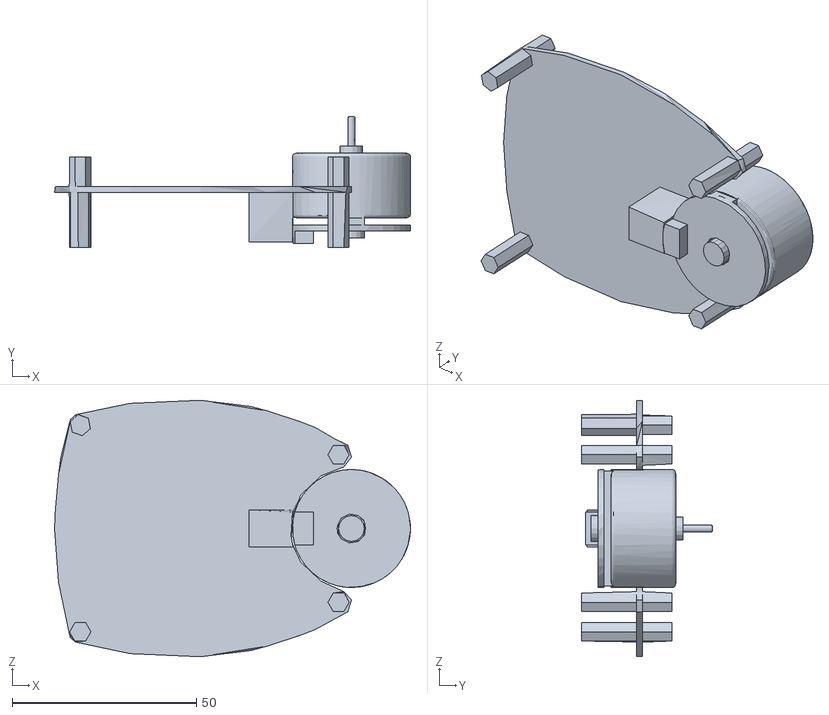
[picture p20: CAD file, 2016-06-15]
src/lidar_robot/models/lidar_bottom.stl
96.5 x 35.6 x 69.5

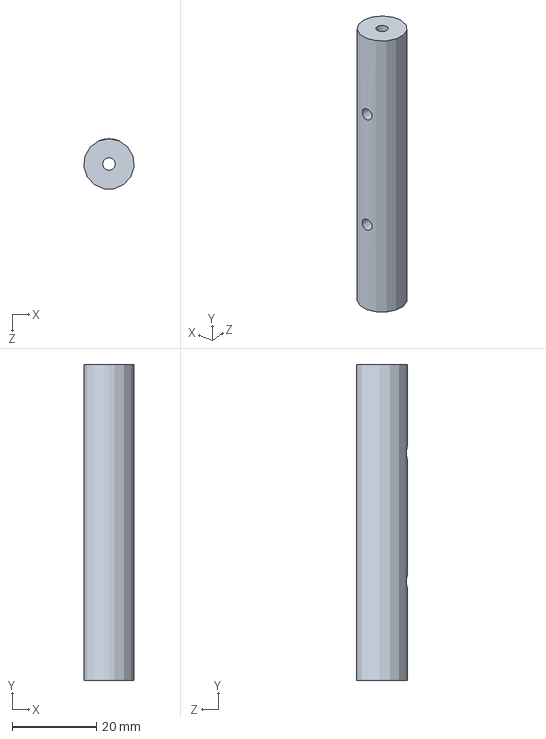
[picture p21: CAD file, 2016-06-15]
CAD/solidworks_model/caster_shaft.SLDPRT
11.9 x 75.0 x 12.0 mm

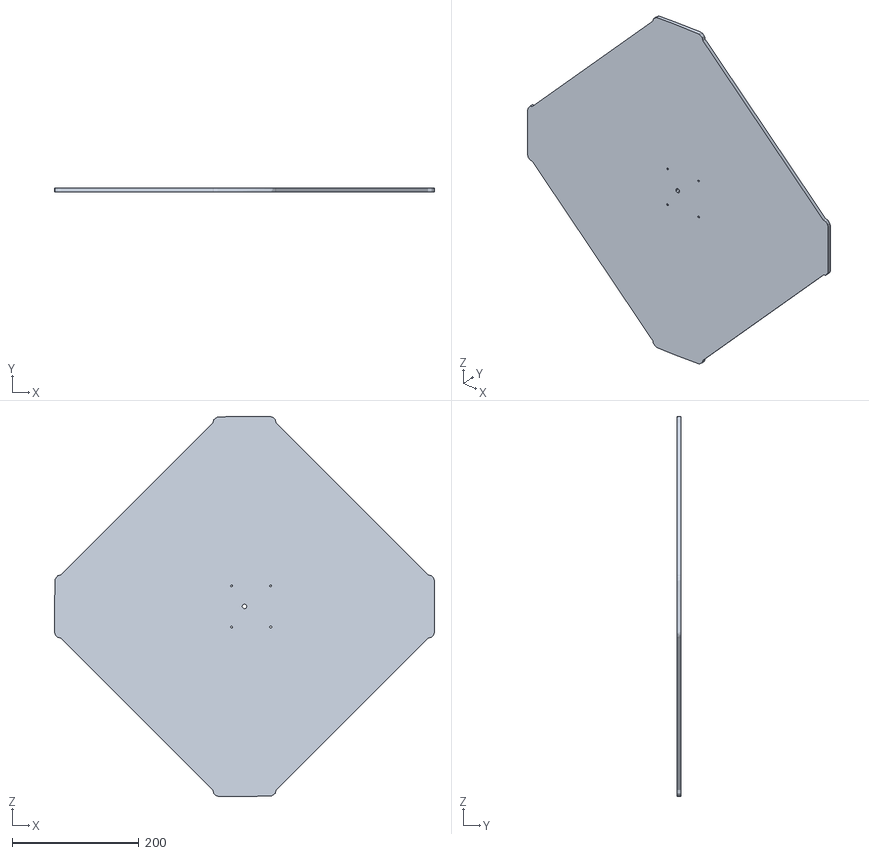
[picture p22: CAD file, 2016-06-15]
src/lidar_robot/models/top_plate.stl
600.0 x 6.00 x 600.0

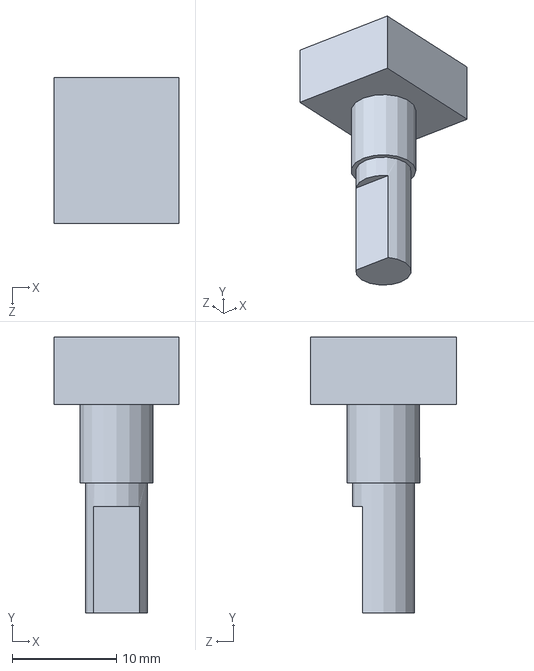
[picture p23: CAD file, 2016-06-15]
CAD/solidworks_model/encoder.SLDPRT
12.0 x 26.5 x 14.0 mm

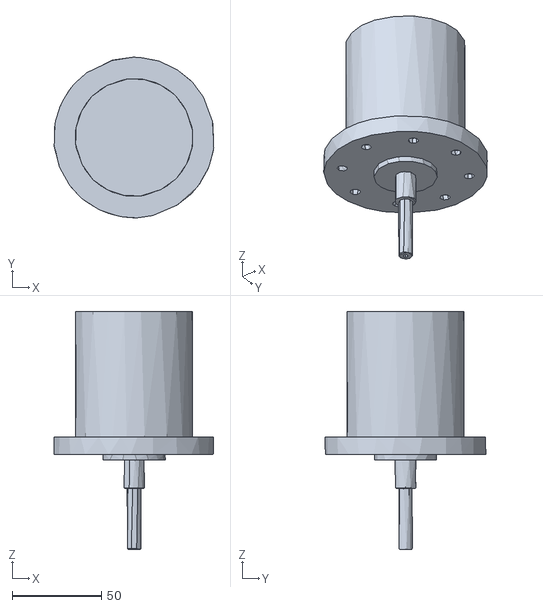
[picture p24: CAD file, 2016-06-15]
src/lidar_robot/models/motor.stl
89.1 x 89.8 x 133.0

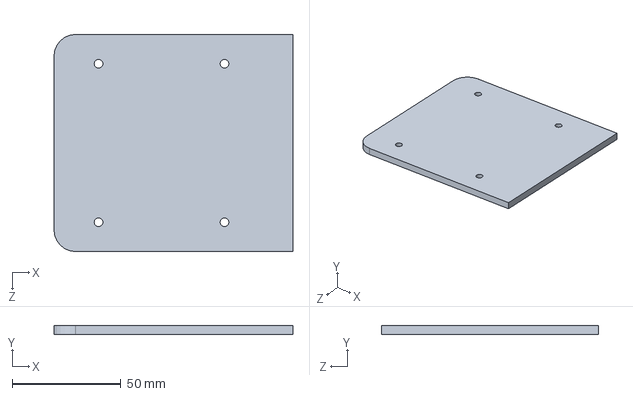
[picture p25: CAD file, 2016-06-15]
CAD/solidworks_model/base_height.SLDPRT
110.0 x 4.00 x 100.0 mm

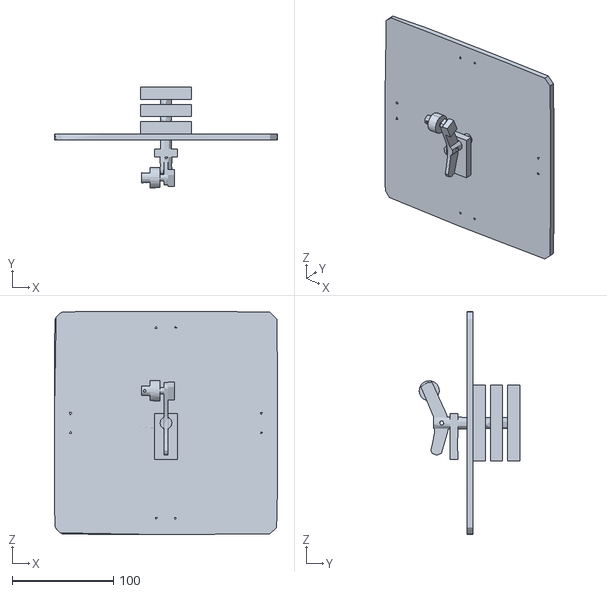
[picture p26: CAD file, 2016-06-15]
src/lidar_robot/models/feedback.stl
220.0 x 99.3 x 220.0

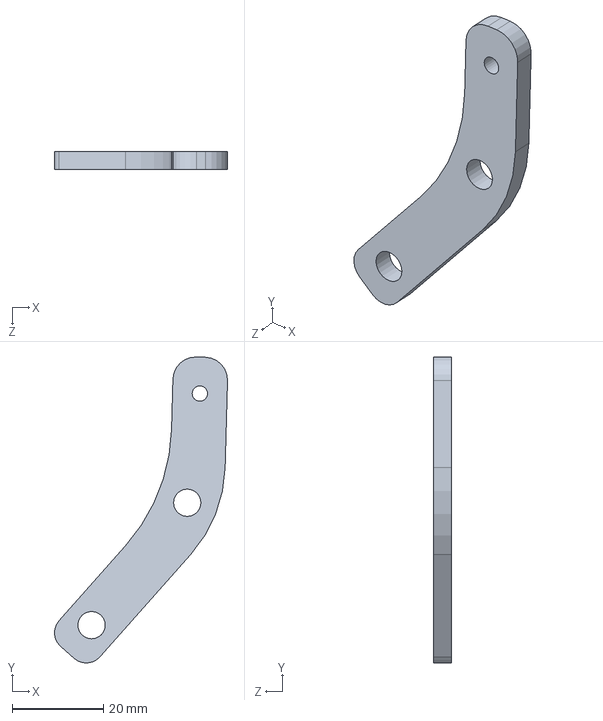
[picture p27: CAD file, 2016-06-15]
CAD/solidworks_model/sidelink.SLDPRT
38.0 x 67.2 x 4.00 mm

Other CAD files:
src/lidar_robot/models/lidar_base.stl
CAD/solidworks_model/Feedback_base.SLDPRT
src/lidar_robot/models/lidar_up.stl
CAD/solidworks_model/circit1.SLDPRT
CAD/solidworks_model/15mm__studSLDPRT.SLDPRT
CAD/solidworks_model/Base Plate.SLDPRT
CAD/solidworks_model/Base Plate1.SLDPRT
CAD/solidworks_model/Lidar.SLDPRT
CAD/solidworks_model/Lower Clamp.sldprt
CAD/solidworks_model/Motor.SLDPRT
CAD/solidworks_model/base_caster.SLDPRT
CAD/solidworks_model/cutbase.SLDPRT
CAD/solidworks_model/l_clamp.SLDPRT
CAD/solidworks_model/lidar_base.SLDPRT
CAD/solidworks_model/shaft.SLDPRT
CAD/solidworks_model/sidelink2.SLDPRT
CAD/solidworks_model/stud15mm.SLDPRT
CAD/solidworks_model/top_ecoder_holder.SLDPRT
CAD/solidworks_model/wheel.SLDPRT
src/lidar_robot/models/base.stl
src/lidar_robot/models/c_clamp.stl
src/lidar_robot/models/circuit_plate.stl
src/lidar_robot/models/motor_shaft.stl

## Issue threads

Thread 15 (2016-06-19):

Send all data from Arduino in a single object

prajankya, 2016-06-19:
Extending The issue of #14

prajankya, 2016-06-19:
The Datatype of the object can be **String**

prajankya, 2016-06-19:
can use multiarray

prajankya, 2016-06-19:
can use Float instead of int as in the following reference
http://answers.ros.org/question/10988/use-multiarray-in-rosserial/

Closed 2016-07-07.

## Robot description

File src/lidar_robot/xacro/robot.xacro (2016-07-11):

<?xml version="1.0"?>
<robot xmlns:xacro="http://www.ros.org/wiki/xacro" name="lidar_robot">
    <xacro:include filename="$(find lidar_robot)/xacro/materials.xacro"/>
    <xacro:property name="c_clamp_dist" value="0.31"/>

    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

    <xacro:macro name="stud" params="myname x y z parent">
        <link name="${myname}">
            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
        </link>
        <joint name="${parent}_${myname}" type="fixed">
            <parent link="${parent}"/>
            <child link="${myname}"/>
        </joint>
    </xacro:macro>

    <xacro:macro name="wheel">
        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
        <inertial>
            <mass value="0.5"/>
            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
        </inertial>
        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
    </xacro:macro>

    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
    <link name="base_link">
        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
        <inertial>
            <mass value="8"/>
            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
        </inertial>
        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
    </link>

    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
    <link name="c_clamp_1">
        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
    </link>
    <joint name="base_c_clamp_1" type="fixed">
        <parent link="base_link"/>
        <child link="c_clamp_1"/>
    </joint>
    <link name="motor_1">
        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
    </link>
    <joint name="c_clamp_motor_1" type="fixed">
        <parent link="c_clamp_1"/>
        <child link="motor_1"/>
    </joint>
    <link name="shaft_1">
        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
    </link>
    <joint name="motor_shaft_1" type="continuous">
        <parent link="base_link"/>
        <child link="shaft_1"/>
        <axis xyz="1 0 0"/>
        <origin xyz="${-(c_clamp_dist+0.01)} 0 0.045" rpy="0 0 ${pi}"/>
    </joint>
    <link name="wheel_1">
        <xacro:wheel/>
    </link>
    <joint name="shaft_wheel_1" type="fixed">
        <parent link="shaft_1"/>
        <child link="wheel_1"/>
    </joint>
    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
    <link name="c_clamp_2">
        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
    </link>
    <joint name="base_c_clamp_2" type="fixed">
        <parent link="base_link"/>
        <child link="c_clamp_2"/>
    </joint>
    <link name="motor_2">
        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
    </link>
    <joint name="c_clamp_motor_2" type="fixed">
        <parent link="c_clamp_2"/>
        <child link="motor_2"/>
    </joint>
    <link name="shaft_2">
        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
    </link>
    <joint name="motor_shaft_2" type="continuous">
        <parent link="base_link"/>
        <child link="shaft_2"/>
        <origin xyz="0 ${(c_clamp_dist+0.01)} 0.045" rpy="0 0 ${pi/2}"/>
    </joint>
    <link name="wheel_2">
        <xacro:wheel/>
    </link>
    <joint name="shaft_wheel_2" type="fixed">
        <parent link="shaft_2"/>
        <child link="wheel_2"/>
    </joint>
    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
    <link name="c_clamp_3">
        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
    </link>
    <joint name="base_c_clamp_3" type="fixed">
        <parent link="base_link"/>
        <child link="c_clamp_3"/>
    </joint>
    <link name="motor_3">
        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
    </link>
    <joint name="c_clamp_motor_3" type="fixed">
        <parent link="c_clamp_3"/>
        <child link="motor_3"/>
    </joint>
    <link name="shaft_3">
        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
    </link>
    <joint name="motor_shaft_3" type="continuous">
        <parent link="base_link"/>
        <child link="shaft_3"/>
        <origin xyz="${(c_clamp_dist+0.01)} 0 0.045" rpy="0 0 0"/>
    </joint>
    <link name="wheel_3">
        <xacro:wheel/>
    </link>
    <joint name="shaft_wheel_3" type="fixed">
        <parent link="shaft_3"/>
        <child link="wheel_3"/>
    </joint>
    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
    <link name="c_clamp_4">
        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
    </link>
    <joint name="base_c_clamp_4" type="fixed">
        <parent link="base_link"/>
        <child link="c_clamp_4"/>
    </joint>
    <link name="motor_4">
        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
    </link>
    <joint name="c_clamp_motor_4" type="fixed">
        <parent link="c_clamp_4"/>
        <child link="motor_4"/>
    </joint>
    <link name="shaft_4">
        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
    </link>
    <joint name="motor_shaft_4" type="continuous">
        <parent link="base_link"/>
        <child link="shaft_4"/>
        <origin xyz="0 ${-(c_clamp_dist+0.01)} 0.045" rpy="0 0 ${-pi/2}"/>
    </joint>
    <link name="wheel_4">
        <xacro:wheel/>
    </link>
    <joint name="shaft_wheel_4" type="fixed">
        <parent link="shaft_4"/>
        <child link="wheel_4"/>
    </joint>
    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
    <link name="top_plate">
        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
    </link>
    <joint name="base_link_top_plate" type="fixed">
        <parent link="base_link"/>
        <child link="top_plate"/>
    </joint>
    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
    <link name="circuit_plate">
        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
    </link>
    <joint name="base_link_circuit_plate" type="fixed">
        <parent link="top_plate"/>
        <child link="circuit_plate"/>
    </joint>
    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
    <link name="feedback">
        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
    </link>
    <joint name="base_link_feedback" type="fixed">
        <parent link="base_link"/>
        <child link="feedback"/>
    </joint>

    <xacro:stud myname="s1" x="0.073" y="0.06" z="0.006" parent="feedback"/>
    <xacro:stud myname="s2" x="-0.073" y="0.06" z="0.006" parent="feedback"/>
    <xacro:stud myname="s3" x="0.073" y="-0.06" z="0.006" parent="feedback"/>
    <xacro:stud myname="s4" x="-0.073" y="-0.06" z="0.006" parent="feedback"/>

    <xacro:stud myname="s5" x="0.06" y="0.0735" z="0.006" parent="feedback"/>
    <xacro:stud myname="s6" x="-0.06" y="0.0735" z="0.006" parent="feedback"/>
    <xacro:stud myname="s7" x="0.06" y="-0.0735" z="0.006" parent="feedback"/>
    <xacro:stud myname="s8" x="-0.06" y="-0.0735" z="0.006" parent="feedback"/>

    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
    <link name="lidar_base">
        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
    </link>
    <joint name="circuit_plate_lidar_base" type="fixed">
        <parent link="circuit_plate"/>
        <child link="lidar_base"/>
    </joint>

    <xacro:stud myname="s9" x="-0.021" y="0.0321" z="0.098" parent="lidar_base"/>
    <xacro:stud myname="s10" x="0.041" y="0.0321" z="0.098" parent="lidar_base"/>
    <xacro:stud myname="s11" x="0.041" y="-0.0321" z="0.098" parent="lidar_base"/>
    <xacro:stud myname="s12" x="-0.021" y="-0.0321" z="0.098" parent="lidar_base"/>

    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
    <link name="lidar_bottom">
        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
    </link>
    <joint name="lidar_base_lidar_bottom" type="fixed">
        <parent link="lidar_base"/>
        <child link="lidar_bottom"/>
    </joint>
    <link name="lidar_up">
        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
    </link>
    <joint name="lidar_bottom_lidar_up" type="fixed">
        <parent link="lidar_bottom"/>
        <child link="lidar_up"/>
    </joint>

    <link name="rplidar_frame">
        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
    </link>
    <joint name="base_link_rplidar_frame" type="fixed">
        <origin xyz="0.0 0 0.16" rpy="0 0 0"/>
        <parent link="base_link"/>
        <child link="rplidar_frame"/>
    </joint>
    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
    <link name="x">
        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
    </link>
    <joint name="base_link_x" type="fixed">
        <parent link="base_link"/>
        <child link="x"/>
    </joint>
    <link name="y">
        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
    </link>
    <joint name="base_link_y" type="fixed">
        <parent link="base_link"/>
        <child link="y"/>
    </joint>
    <link name="imu">
        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
    </link>
    <joint name="base_link_imu" type="fixed">
        <parent link="base_link"/>
        <child link="imu"/>
    </joint>
</robot>

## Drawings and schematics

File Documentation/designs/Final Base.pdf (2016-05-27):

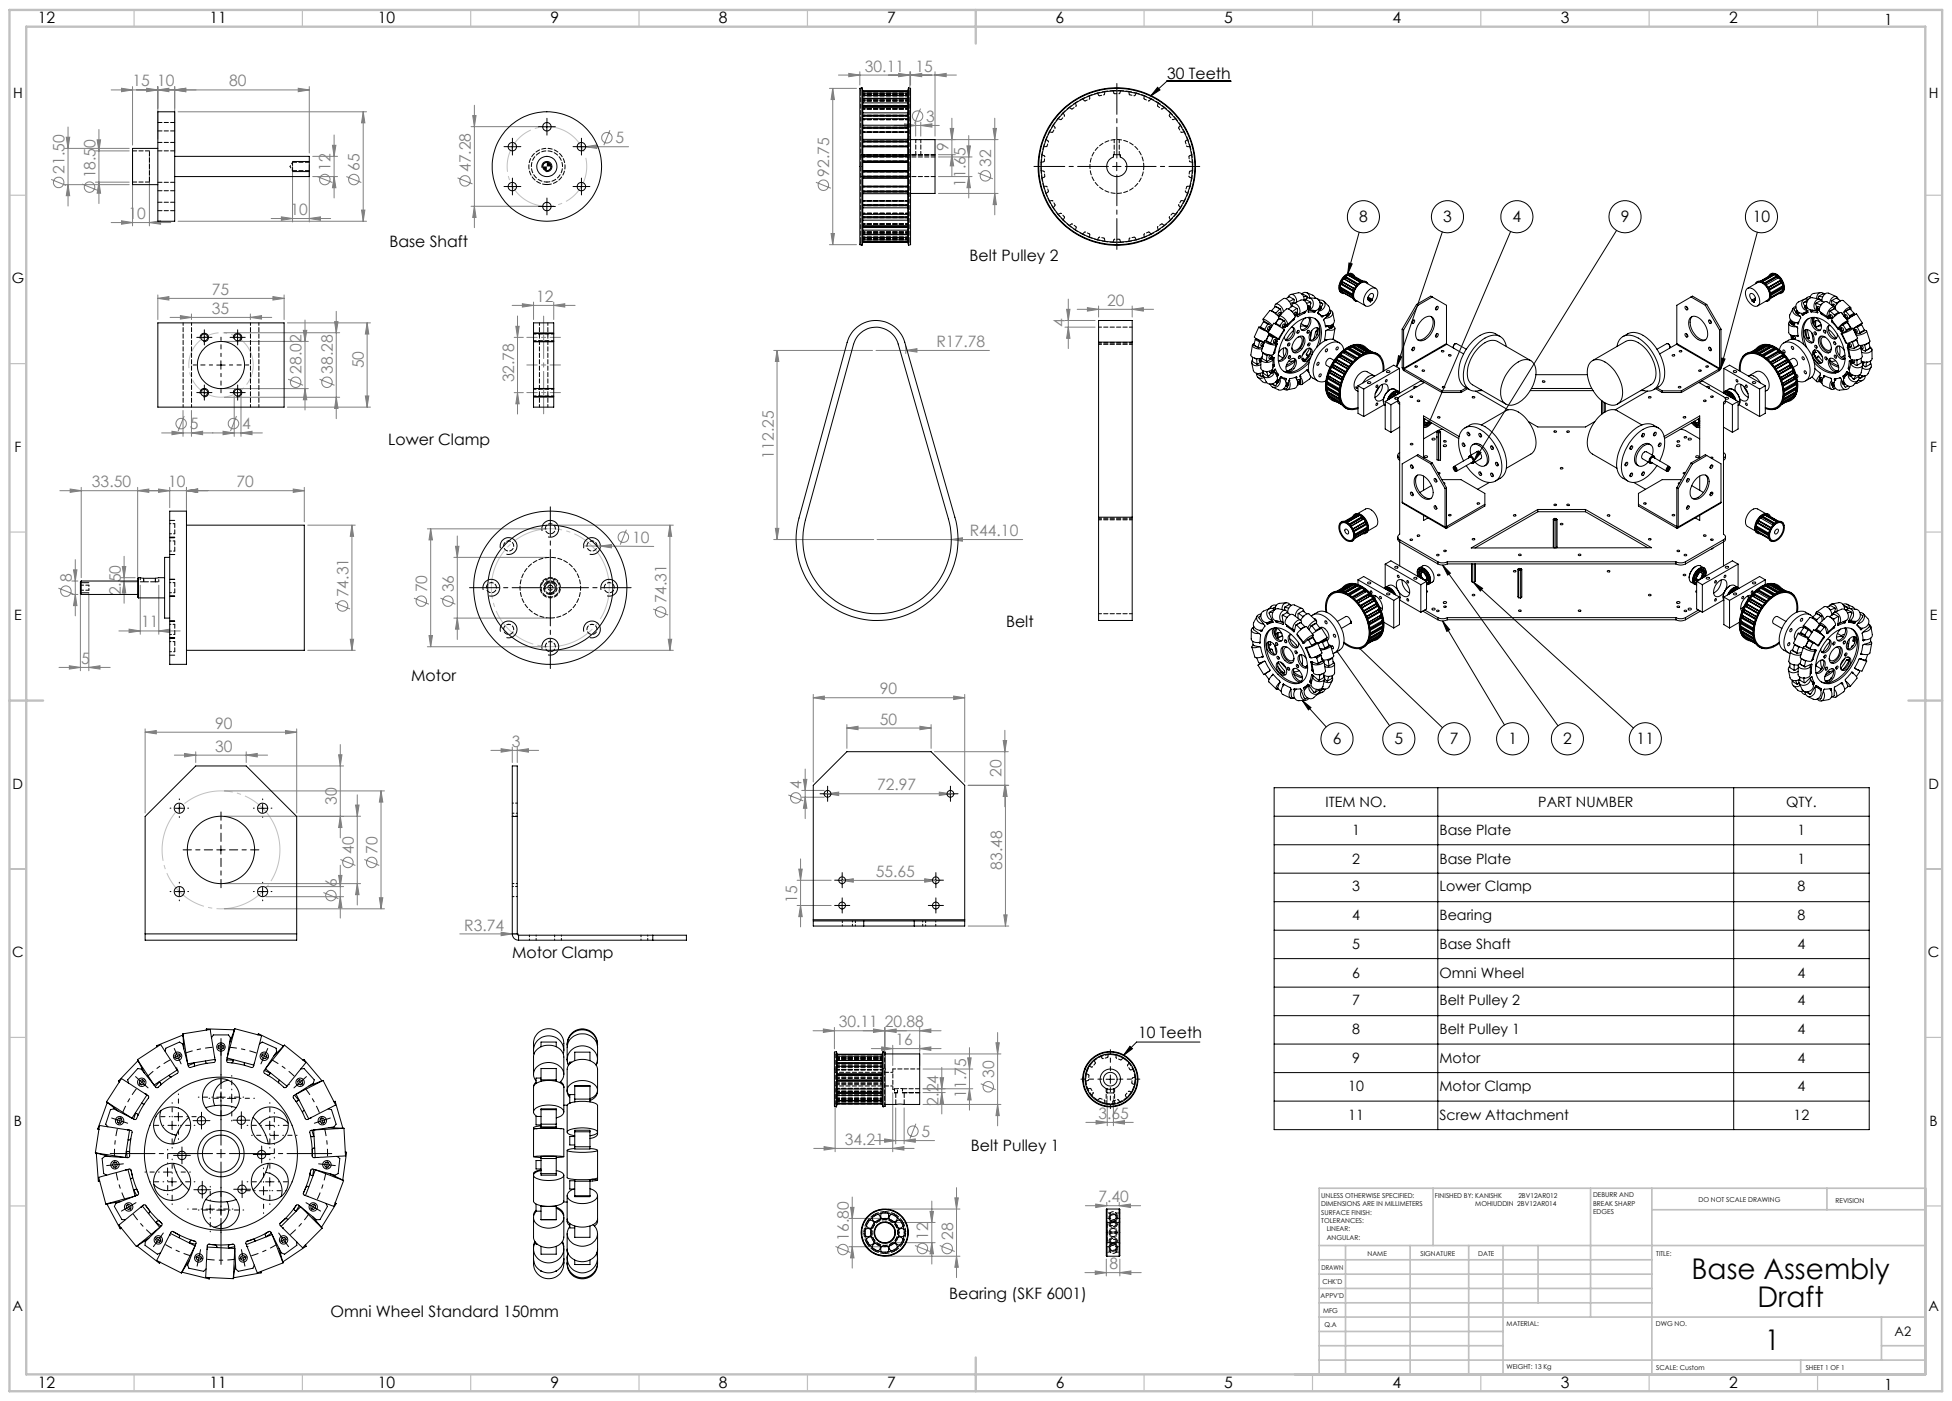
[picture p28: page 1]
Belt Pulley 2; Base Shaft; 10 Teeth; 30 Teeth; Lower Clamp; Motor Clamp; Belt Pulley 1; Bearing (SKF 6001); FINISHED BY: KANISHK; MOHIUDDIN 2BV12AR014; DEBURR AND BREAK SHARP; DO NOT SCALE DRAWING; REVISION; SCALE: Custom; SHEET 1 OF 1; WEIGHT: 13 Kg

ITEM NO. | PART NUMBER | QTY.
1 | Base Plate | 1
2 | Base Plate | 1
3 | Lower Clamp | 8
4 | Bearing | 8
5 | Base Shaft | 4
6 | Omni Wheel | 4
7 | Belt Pulley 2 | 4
8 | Belt Pulley 1 | 4
9 | Motor | 4
10 | Motor Clamp | 4
11 | Screw Attachment | 12

UNLESS OTHERWISE SPECIFIED:
DIMENSIONS ARE IN MILLIMETERS
SURFACE FINISH:
TOLERANCES:
LINEAR:
ANGULAR:

NAME | SIGNATURE | DATE | | | | TITLE: Base Assembly Draft

DRAWN
CHK'D
APPV'D
MFG
Q.A | | | | MATERIAL: | DWG NO. 1 | A2

Omni Wheel Standard 150mm

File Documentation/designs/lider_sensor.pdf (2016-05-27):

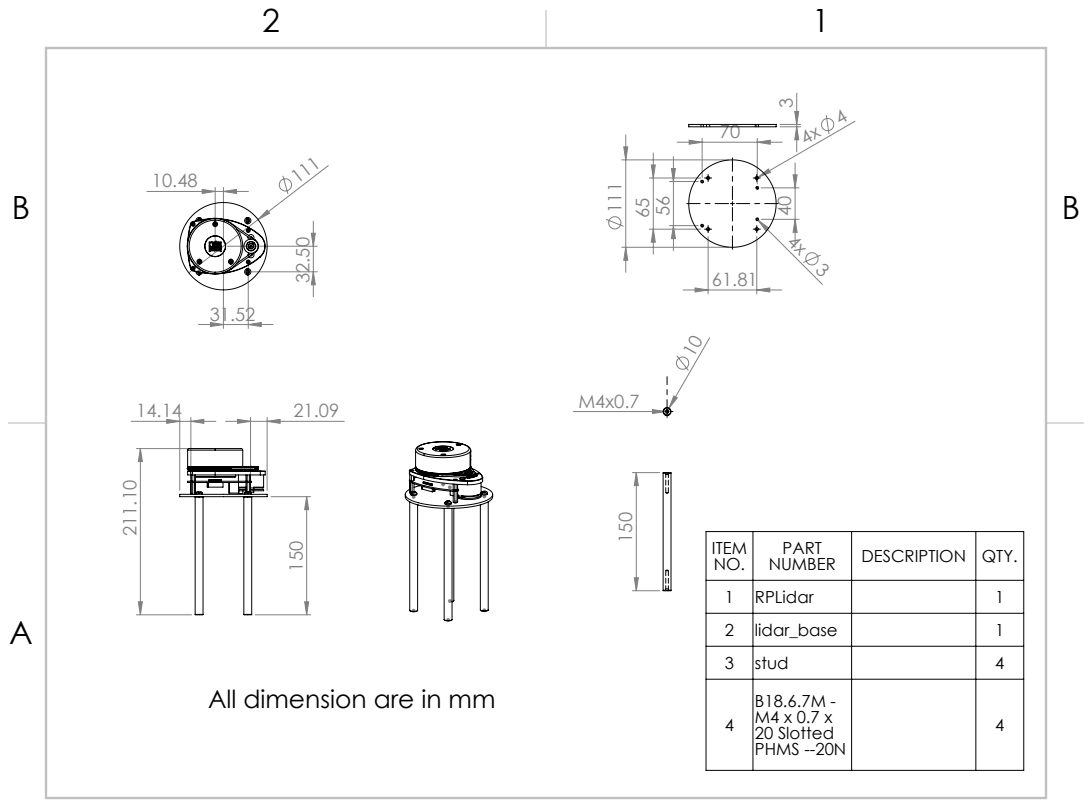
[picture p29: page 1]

ITEM NO. | PART NUMBER | DESCRIPTION | QTY.

1 | RPLidar | | 1
2 | lidar_base | | 1
3 | stud | | 4
4 | B18.6.7M -M4 x 0.7 x 20 Slotted PHMS --20N | | 4

All dimension are in mm

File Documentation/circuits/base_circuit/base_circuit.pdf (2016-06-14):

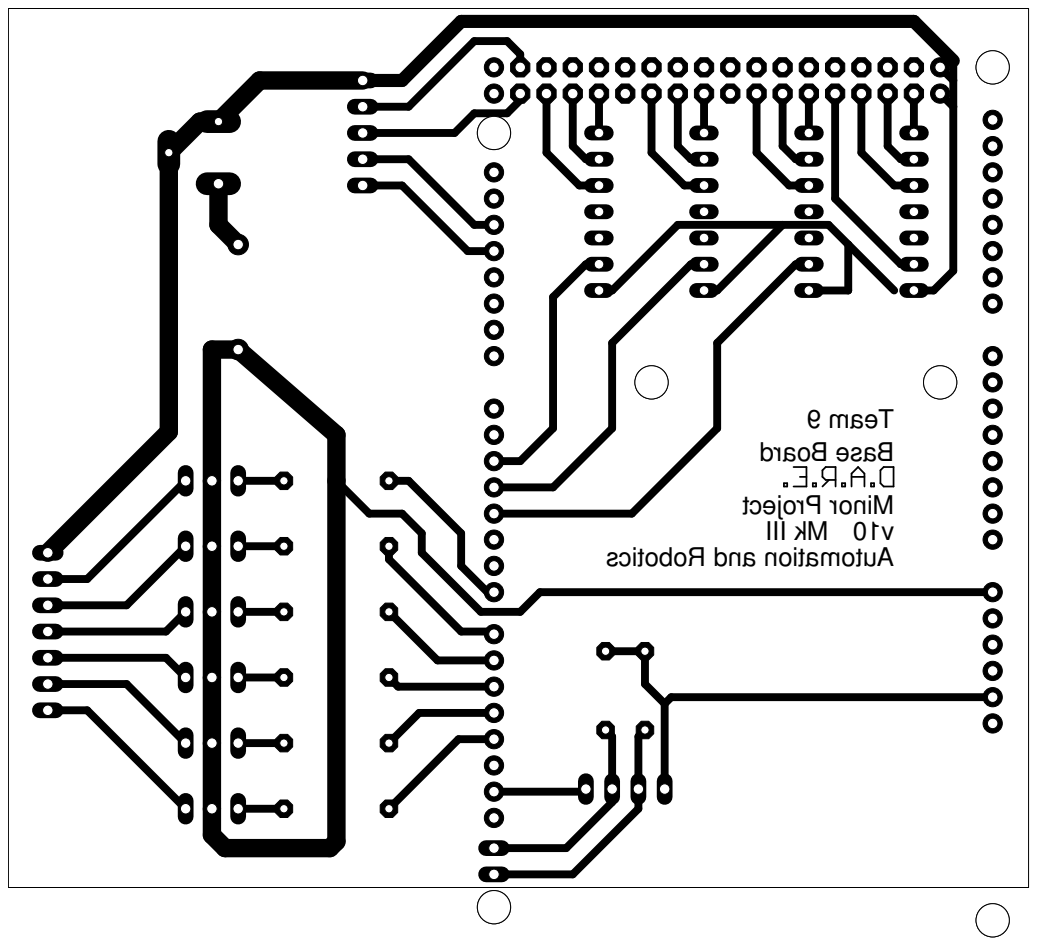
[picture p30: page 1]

t cej or Pr oni M

scit obo Rdna noit a mot uA

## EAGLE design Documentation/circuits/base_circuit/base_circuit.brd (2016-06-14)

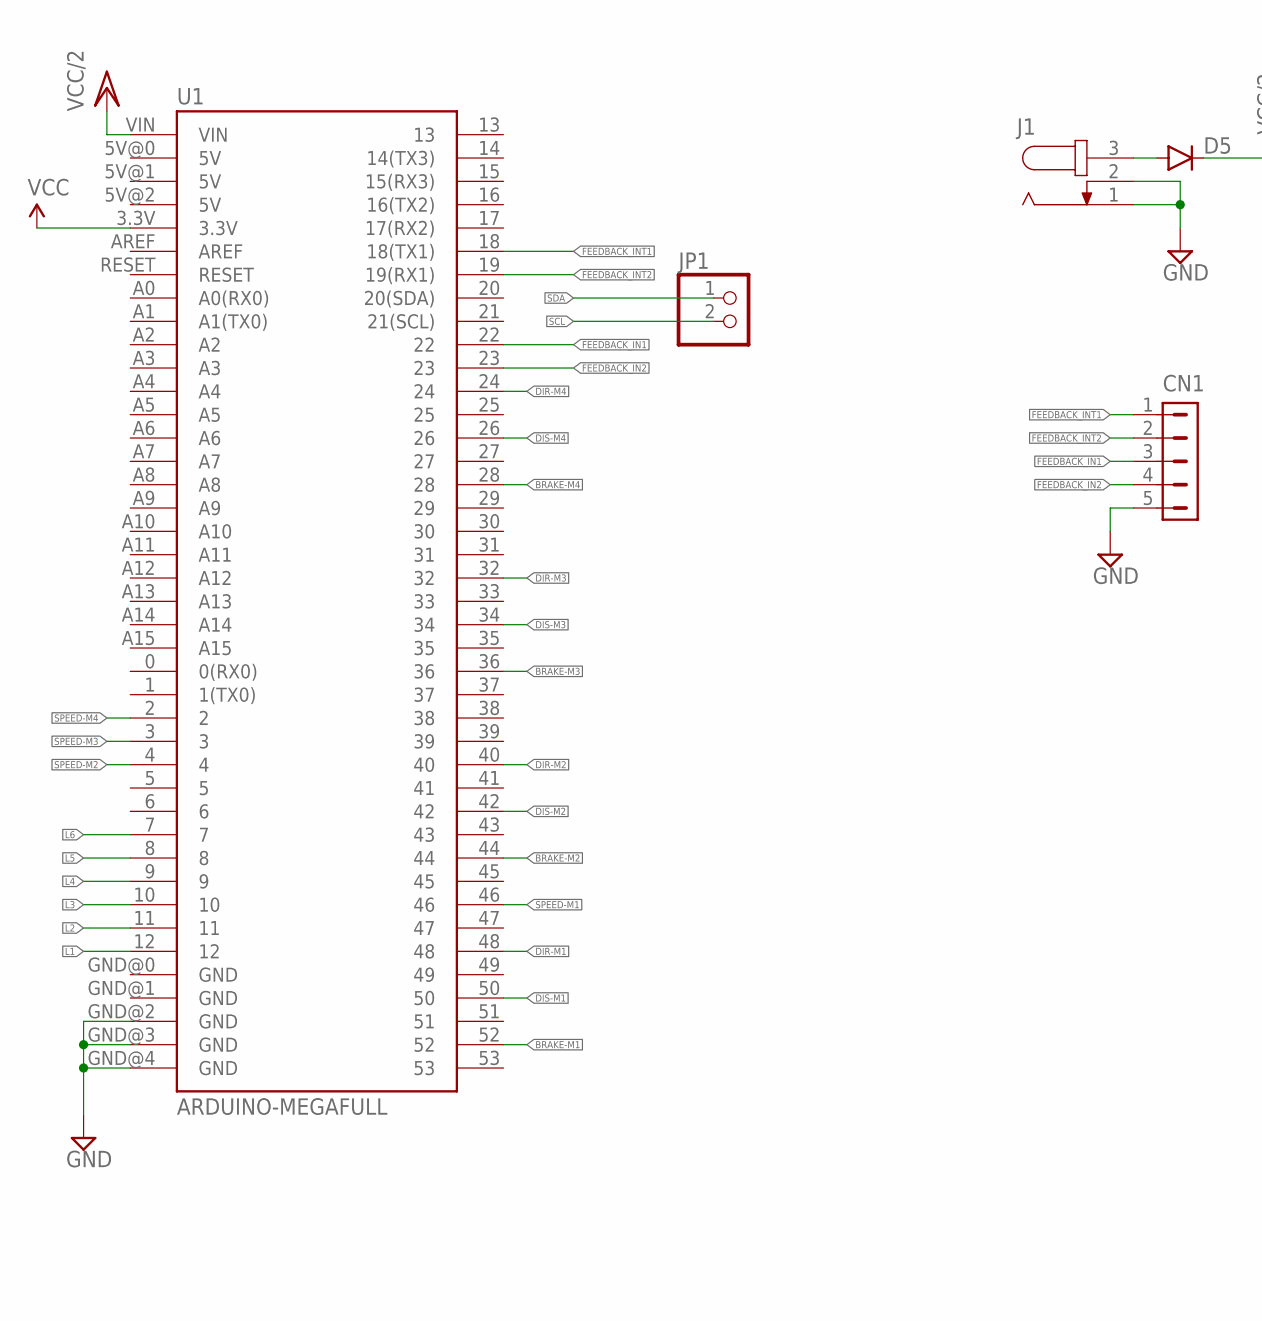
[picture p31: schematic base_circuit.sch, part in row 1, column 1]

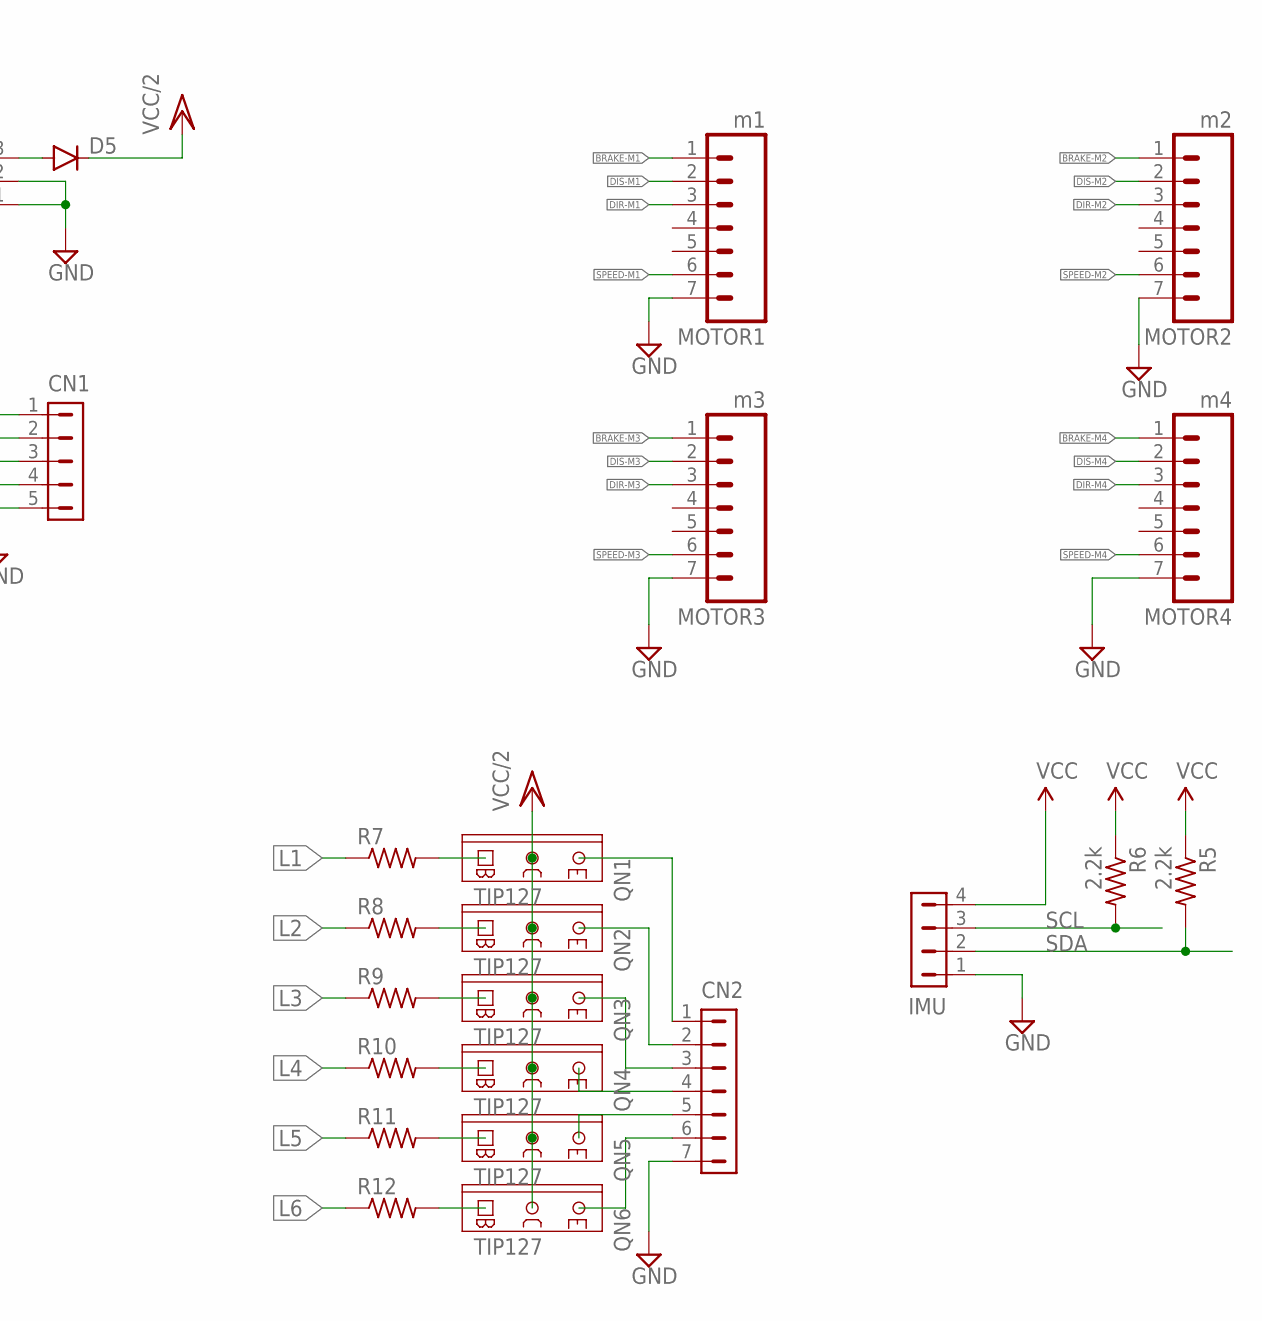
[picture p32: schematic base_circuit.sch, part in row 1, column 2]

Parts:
CN1: HDR-1X5-MTE-100-L; MTE-100-5VL
CN2: HDR-1X7-70543-?; 70543-07
D5: DIODEPTH; DIODE-1N4001
IMU: HDR-1X4-70543-?; 70543-04
J1: JACK-PLUG1; SPC4078
JP1: PINHD-1X2; 1X02
MOTOR1: m1; 07P
MOTOR2: m2; 07P
MOTOR3: m3; 07P
MOTOR4: m4; 07P
QN1, QN2, QN3, QN4, QN5, QN6: TIP127; TO220AV
R5, R6: 2.2k; 0204/7
R7, R8, R9, R10, R11, R12: R-US_0207/10; 0207/10
U1: ARDUINO-MEGAFULL; ARDUINO_MEGA

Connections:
BRAKE-M1: MOTOR1.1, U1.52
BRAKE-M2: MOTOR2.1, U1.44
BRAKE-M3: MOTOR3.1, U1.36
BRAKE-M4: MOTOR4.1, U1.28
DIR-M1: MOTOR1.3, U1.48
DIR-M2: MOTOR2.3, U1.40
DIR-M3: MOTOR3.3, U1.32
DIR-M4: MOTOR4.3, U1.24
DIS-M1: MOTOR1.2, U1.50
DIS-M2: MOTOR2.2, U1.42
DIS-M3: MOTOR3.2, U1.34
DIS-M4: MOTOR4.2, U1.26
FEEDBACK_IN1: CN1.3, U1.22
FEEDBACK_IN2: CN1.4, U1.23
FEEDBACK_INT1: CN1.1, U1.18 (18(TX1))
FEEDBACK_INT2: CN1.2, U1.19 (19(RX1))
GND: CN1.5, CN2.7, IMU.1, J1.1, J1.2, MOTOR1.7, MOTOR2.7, MOTOR3.7, MOTOR4.7, U1.GND@2 (GND), U1.GND@3 (GND), U1.GND@4 (GND)
L1: R7.1, U1.12
L2: R8.1, U1.11
L3: R9.1, U1.10
L4: R10.1, U1.9
L5: R11.1, U1.8
L6: R12.1, U1.7
unnamed: QN1.B, R7.2
unnamed: QN2.B, R8.2
unnamed: QN3.B, R9.2
unnamed: QN4.B, R10.2
unnamed: QN5.B, R11.2
unnamed: QN6.B, R12.2
unnamed: D5.A, J1.3
unnamed: CN2.1, QN1.E
unnamed: CN2.2, QN2.E
unnamed: CN2.3, QN3.E
unnamed: CN2.4, QN4.E
unnamed: CN2.5, QN5.E
unnamed: CN2.6, QN6.E
SCL: IMU.3, JP1.2, R6.2
SDA: IMU.2, JP1.1, R5.2
SPEED-M1: MOTOR1.6, U1.46
SPEED-M2: MOTOR2.6, U1.4
SPEED-M3: MOTOR3.6, U1.3
SPEED-M4: MOTOR4.6, U1.2
VCC: IMU.4, R5.1, R6.1, U1.3.3V
VCC/2: D5.C, QN1.C, QN2.C, QN3.C, QN4.C, QN5.C, QN6.C, U1.VIN

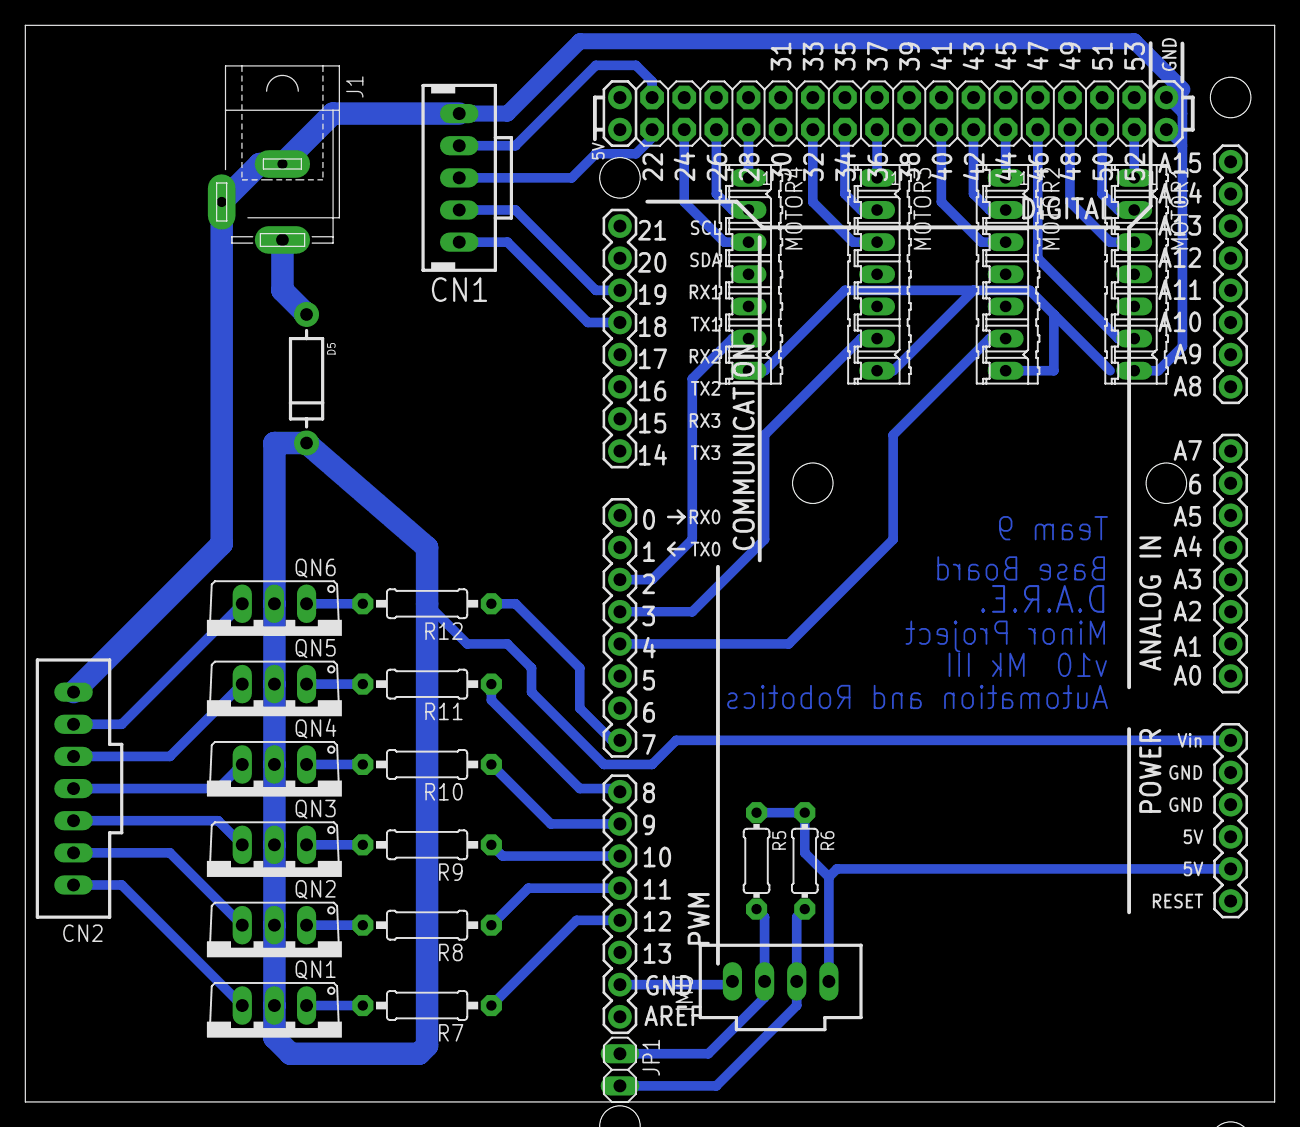
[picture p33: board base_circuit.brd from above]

Board: 2 copper layers, 98.7 x 85.1 mm, 25 parts (0 on the bottom side), 44 nets.

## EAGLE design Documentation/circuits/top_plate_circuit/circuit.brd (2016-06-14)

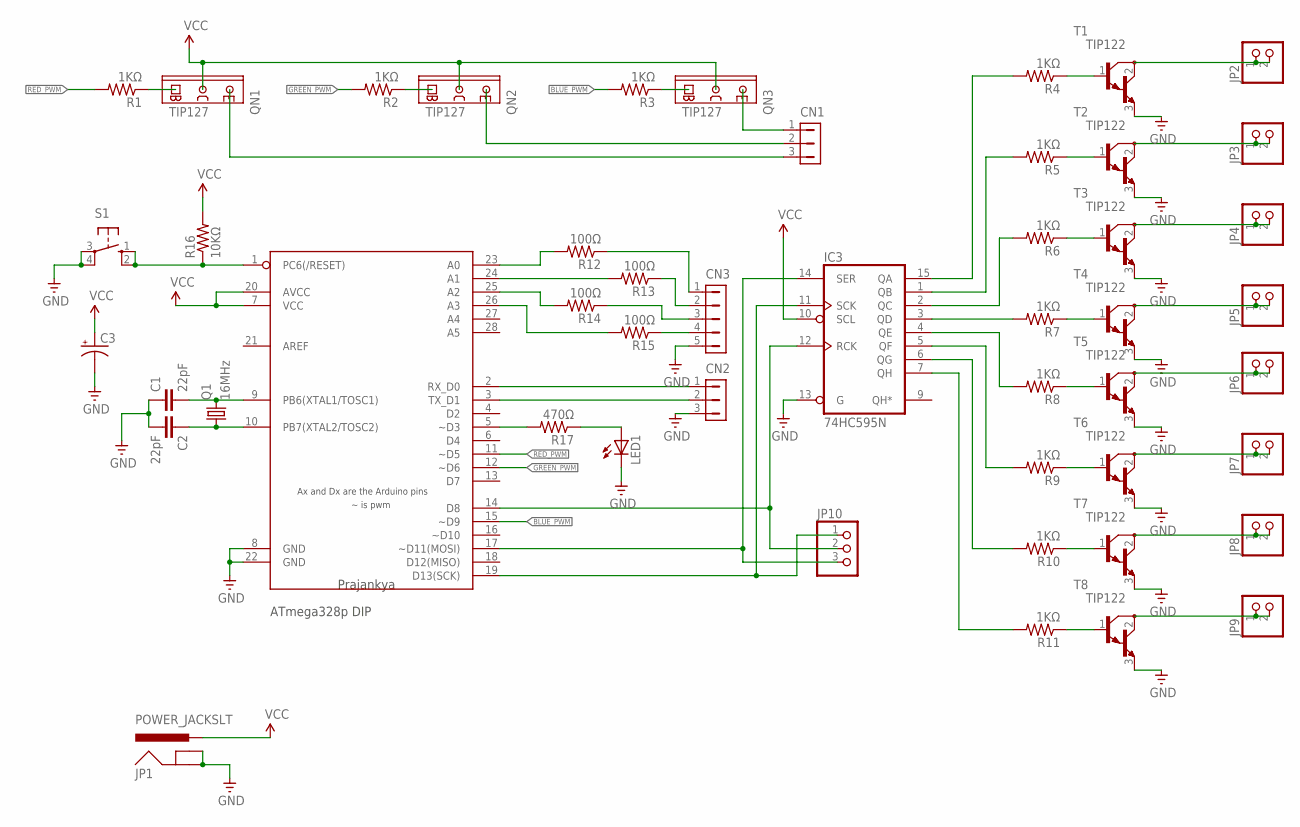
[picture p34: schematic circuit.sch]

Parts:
C1, C2: 22pF; C025-025X050
C3: CPOL-USTT2D6L; TT2D6L
CN1, CN2: HDR-1X3-70543-?; 70543-03
CN3: HDR-1X5-70543-?; 70543-05
IC3: 74HC595N; DIL16
JP1: POWER_JACKSLT; POWER_JACK_SLOT
JP2, JP3, JP4, JP5, JP6, JP7, JP8, JP9: PINHD-1X2; 1X02
JP10: PINHD-1X3; 1X03
LED1: LED5MM
Q1: 16MHz; HC49U-V
QN1, QN2, QN3: TIP127; TO220AV
R1, R2, R3, R4, R5, R6, R7, R8, R9, R10, R11: 1KΩ; AXIAL-0.4
R12, R13, R14, R15: 100Ω; AXIAL-0.4
R16: 10KΩ; 0207/10
R17: 470Ω; 0207/12
S1: 10-XX; B3F-10XX
T1, T2, T3, T4, T5, T6, T7, T8: TIP122; TO220
U$1: ATMEGA328P_DIP; ATMEGA328_CUSTOMPAD

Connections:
BLUE_PWM: R3.P$2 (2), U$1.15 (~D9)
GND: C1.1, C2.2, C3.-, CN2.3, CN3.5, IC3.8 (GND), IC3.13 (G), JP1.GND@1 (GNDBREAK), JP1.GND@2 (GND), LED1.K (C), S1.3, S1.4 (P1), T1.3 (E), T2.3 (E), T3.3 (E), T4.3 (E), T5.3 (E), T6.3 (E), T7.3 (E), T8.3 (E), U$1.8 (GND), U$1.22 (GND)
GREEN_PWM: R2.P$2 (2), U$1.12 (~D6)
N1: JP2.1, JP2.2, T1.2 (C)
N2: JP3.1, JP3.2, T2.2 (C)
N3: JP4.1, JP4.2, T3.2 (C)
N4: JP5.1, JP5.2, T4.2 (C)
N5: JP6.1, JP6.2, T5.2 (C)
N6: JP7.1, JP7.2, T6.2 (C)
N7: JP8.1, JP8.2, T7.2 (C)
N8: JP9.1, JP9.2, T8.2 (C)
unnamed: CN1.3, QN1.E
unnamed: CN1.2, QN2.E
unnamed: CN1.1, QN3.E
unnamed: QN1.B, R1.P$1 (1)
unnamed: QN2.B, R2.P$1 (1)
unnamed: QN3.B, R3.P$1 (1)
unnamed: R4.P$1 (1), T1.1 (B)
unnamed: R5.P$1 (1), T2.1 (B)
unnamed: R12.P$2 (2), U$1.23 (A0)
unnamed: IC3.15 (QA), R4.P$2 (2)
unnamed: R13.P$2 (2), U$1.24 (A1)
unnamed: IC3.1 (QB), R5.P$2 (2)
unnamed: R6.P$1 (1), T3.1 (B)
unnamed: R14.P$2 (2), U$1.25 (A2)
unnamed: IC3.2 (QC), R6.P$2 (2)
unnamed: R7.P$1 (1), T4.1 (B)
unnamed: R15.P$2 (2), U$1.26 (A3)
unnamed: IC3.3 (QD), R7.P$2 (2)
unnamed: R8.P$1 (1), T5.1 (B)
unnamed: CN2.1, U$1.2 (RX_D0)
unnamed: IC3.4 (QE), R8.P$2 (2)
unnamed: R9.P$1 (1), T6.1 (B)
unnamed: CN2.2, U$1.3 (TX_D1)
unnamed: IC3.5 (QF), R9.P$2 (2)
unnamed: R10.P$1 (1), T7.1 (B)
unnamed: R17.2, U$1.5 (~D3)
unnamed: IC3.6 (QG), R10.P$2 (2)
unnamed: R11.P$1 (1), T8.1 (B)
unnamed: LED1.A, R17.1
unnamed: IC3.7 (QH), R11.P$2 (2)
unnamed: IC3.11 (SCK), JP10.1, U$1.19 (D13(SCK))
unnamed: IC3.12 (RCK), JP10.2, U$1.14 (D8)
unnamed: C2.1, Q1.1, U$1.10 (PB7(XTAL2/TOSC2))
unnamed: C1.2, Q1.2, U$1.9 (PB6(XTAL1/TOSC1))
unnamed: CN3.1, R12.P$1 (1)
unnamed: CN3.2, R13.P$1 (1)
unnamed: CN3.3, R14.P$1 (1)
unnamed: CN3.4, R15.P$1 (1)
unnamed: IC3.14 (SER), JP10.3, U$1.17 (~D11(MOSI))
unnamed: R16.1, S1.1 (S), S1.2 (S1), U$1.1 (PC6(/RESET))
RED_PWM: R1.P$2 (2), U$1.11 (~D5)
VCC: C3.+, IC3.10 (SCL), IC3.16 (VCC), JP1.PWR, QN1.C, QN2.C, QN3.C, R16.2, U$1.7 (VCC), U$1.20 (AVCC)

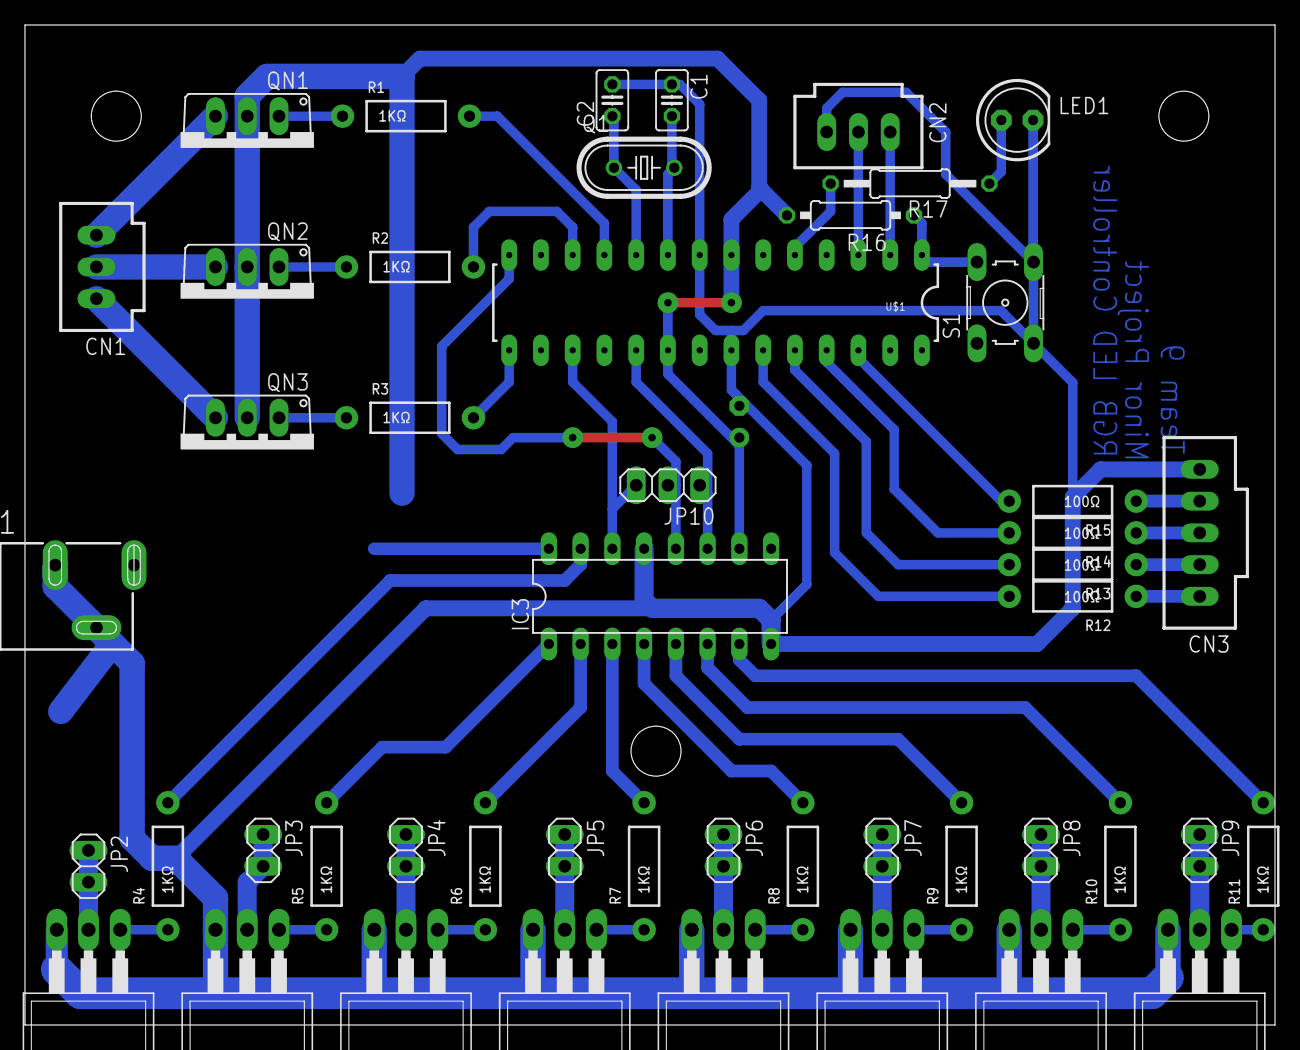
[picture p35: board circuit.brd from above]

Board: 2 copper layers, 100.0 x 80.0 mm, 49 parts (1 on the bottom side), 53 nets.

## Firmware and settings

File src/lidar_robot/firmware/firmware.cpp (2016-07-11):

//#define USE_DESIGN
#define USE_BASE
#define USE_DEBUG

#include <Arduino.h>
#include <ros.h>
#include <ros/time.h>
#include <std_msgs/String.h>
#include "BLDCOmni.h"

#ifdef USE_DESIGN
#include <rosserial_arduino/Test.h>
#include "Design.h"
Design design;
using rosserial_arduino::Test;
void animate_Design_callback(const Test::Request & req, Test::Response & res){
  String s = String(req.input);
  int type = s.toInt();
  design.animate(type);
}
ros::ServiceServer<Test::Request, Test::Response> server("animate_Design",&animate_Design_callback);
#endif

#ifdef USE_BASE
BLDCOmni base;
int brake_ = 0;
int dir_ = 5;
int mag_ = 0;
bool brake = false;

void messageCb(const std_msgs::String &_cmd) {
  String ss = ((const char * ) _cmd.data);
  char s[ss.length() + 1];
  ss.toCharArray(s, ss.length() + 1);

  char *p = s;
  dir_ = String(strtok_r(p, ",", &p)).toInt();
  mag_ = String(strtok_r(p, ",", &p)).toInt();
  brake_ = String(strtok_r(p, ",", &p)).toInt();
}

ros::Subscriber<std_msgs::String> base_sub("base_command", messageCb);
#endif

ros::NodeHandle nh;

#ifdef USE_DEBUG
std_msgs::String str_msg;
ros::Publisher pub3("debug_out", &str_msg);
#endif

void setup() {// ----------------------------------------- setup
  nh.initNode();
#ifdef USE_DEBUG
  nh.advertise(pub3);
#endif

#ifdef USE_DESIGN
  design.init(7, 8, 9, 10, 11, 12);//L1, L2, L3, L4, L5, L6
  nh.advertiseService(server);
#endif

#ifdef USE_BASE
  nh.subscribe(base_sub);

  base.setMotor1(46, 50, 48, 52, 1); //speedPin, disablePin, directionPin, brakePin, speedFactor
  base.setMotor2(4, 42, 40, 44, 1);
  base.setMotor3(3, 34, 32, 36, 1);
  base.setMotor4(2, 26, 24, 28, 1);

  base.setDir(5);
  base.setMag(0);
#endif
}

void loop() {
#ifdef USE_DEBUG
  String s = "dir = " + String(dir_) + "  mag=" + String(mag_) + " brake= " + String(brake_);
  char bb3[50];
  s.toCharArray(bb3, 50);
  str_msg.data = bb3;
  pub3.publish(&str_msg);
#endif

  nh.spinOnce();

#ifdef USE_BASE
  if (brake_ && !brake) {
    base.brakeOn();
    brake = true;
  }

  if (brake && !brake_) {
    base.brakeOff();
    brake = false;
  }

  base.setDir(dir_);
  base.setMag(mag_);
#endif

  delay(10);
}

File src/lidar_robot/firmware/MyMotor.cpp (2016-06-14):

#include<Arduino.h>
#include"MyMotor.h"


void MyMotor::init(int _speedPin, int _disablePin, int _directionPin, int _brakePin, float _correctionFactor) {
  speedPin = _speedPin;
  disablePin = _disablePin;
  directionPin = _directionPin;
  brakePin = _brakePin;
  correctionFactor = _correctionFactor;

  pinMode(disablePin, OUTPUT);
  pinMode(directionPin, OUTPUT);
  pinMode(brakePin, OUTPUT);
}

void MyMotor::acw() {
  digitalWrite(directionPin, LOW);
  digitalWrite(disablePin, HIGH);
}

void MyMotor::cw() {
  digitalWrite(directionPin, HIGH);
  digitalWrite(disablePin, HIGH);
}

void MyMotor::off() {
  digitalWrite(disablePin, LOW);
}

void MyMotor::setMag(int _mag) {
  analogWrite(speedPin, constrain(round(correctionFactor * _mag), 0, 255));
}

void MyMotor::brakeOn() {
  digitalWrite(brakePin, HIGH);
}
void MyMotor::brakeOff() {
  digitalWrite(brakePin, LOW);
}

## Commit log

2016-04-03 v1 of Base circuit
    [base_circuit.brd, base_circuit.sch]
2016-04-03 deleted electronics as it is added in the individual repo of base
    [base_circuit.brd, base_circuit.sch]
2016-04-04 Removed Electronics and Programming folders as they are going in the Dedicated repositories
    [base_circuit.brd, base_circuit.sch]
2016-04-04 solved scratch compiling closed #1
    [firmware.cpp]
2016-04-05 Working towards #4 , added led pins
2016-04-05 Added circuits folder closed #6
    [base_circuit.brd, base_circuit.sch, circuit.brd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]
2016-04-06 updated Circuit
2016-04-06 changed the whole circuit to use speed control for individula motors and also added connections for top plate design leds
    [base_circuit.brd, base_circuit.sch]
2016-04-08 edited BRD file
    [base_circuit.brd]
2016-04-08 Edited the base program to take new speed and brake control
2016-04-09 added top plate design program functions closed #15
2016-04-09 added led functions
2016-04-09 added outIn LED function
2016-04-16 Updated Odometry output
2016-04-21 Added Design Service closed #16 , changed IMU use to a separate cpp, making it optional with one declare closed #19
2016-04-29 Verified the problem with led design
    [firmware.cpp]
2016-04-30 Updated URDF tf_broadcaster
2016-04-30 Adding v2 Models
    [15mm__studSLDPRT.SLDPRT, Base Plate.SLDPRT, Base Plate1.SLDPRT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]
2016-04-30 testing with base speed pwm problem
    [MyMotor.cpp, firmware.cpp]
2016-04-30 Repaired Speed Problem, closed #24
    [Design.cpp, firmware.cpp]
2016-04-30 Repaired Different motor speed Problem, closed #24
    [BLDCOmni.cpp, Design.cpp, firmware.cpp]
2016-05-01 Repaired speed problem of motors
    [BLDCOmni.cpp, firmware.cpp]
2016-05-02 Added magnetometer heading in between
2016-05-27 Added rendered images in CAD Models
2016-06-14 Moved to src
    [base.rviz.xacro, base_circuit.brd, base_circuit.sch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]
2016-06-14 added Meshes
    [base.rviz.xacro, base.stl, base.xacro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]
2016-06-15 Updated Solidworks Models v3
    [Base Plate.SLDPRT, Base Plate1.SLDPRT, Feedback_base.SLDPRT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]
2016-06-15 Tiding the repo
    [15mm__studSLDPRT.SLDPRT, Base Plate.SLDPRT, Base Plate1.SLDPRT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]
2016-06-15 Moved circuits to Documentation
    [base_circuit.brd, base_circuit.sch, circuit.brd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]
2016-06-15 Added STL and PLY models in CAD
    [Omni_Whee23l.ply, base.stl, c_clamp.stl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]
2016-06-15 updates to RPlidar
    [base.xacro]
2016-06-15 Moved Models in the ros package for xacro discovery
    [Omni_Whee23l.ply, base.stl, c_clamp.stl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]
2016-06-15 Base model Down scaled
    [base.stl]
2016-06-15 further scaled down to 0.01x
    [base.stl]
2016-06-15 further scaled down to 0.001x
    [base.stl]
2016-06-15 Scaled back up the base
    [base.stl]
2016-06-15 added c clamp and shaft to the xacro
    [robot.xacro, wheels.ply]
2016-06-15 Added dae of wheel and removed unrequired files
    [wheels.ply]
2016-06-15 setting wheel
    [robot.xacro]
2016-06-15 Added wheel collada with texture
2016-06-15 updating robot.xacro
    [robot.xacro]
2016-06-15 updating robot.xacro second wheel
    [robot.xacro]
2016-06-16 Added Top Plate to URDF
    [robot.xacro]
2016-06-16 Added circuit plate
    [robot.xacro]
2016-06-16 Updated server.js for spawn, printing stdout and stderr now
    [robot.xacro]
2016-06-16 Changed distance from center Changed distance from center of c clamp motor shaft and wheel to a variable
    [robot.xacro]
2016-06-16 Added Feedback and Studs for it
    [robot.xacro]
2016-06-16 Added RPlidar base in model
    [robot.xacro]
2016-06-16 Added RPlidar Bottom
    [robot.xacro]
2016-06-16 Added Lidar UP updated stud.stl with proper binary encoding
    [robot.xacro, stud.stl]
2016-06-16 Updated RVIZ
    Files working with tf jointstatepublisher and robot_tf_publisher perfectly on rviz as well as website
    [rviz.xacro]
2016-06-17 Cleaned a lot
    [base.xacro, robot.xacro, rviz.xacro]
2016-06-17 Added Gazebo
    [robot.xacro]
2016-06-17 Updated URDF with Gazebo wheels
    [robot.xacro]
2016-06-17 Gazebo is functioning
    [robot.xacro]
2016-06-18 Added ROS-Control
    Partially added, gazebo model does not place shaft correctly yet.
    [lidar_robot_control.yaml, materials.xacro, robot.xacro]
2016-06-18 Removed Controller setup
    Removed controller as the real bot does not have any feedback on wheels, so cannot use the PID control, though gazebo provides it.
    [lidar_robot_control.yaml, robot.xacro]
2016-06-18 Working Gazebo and rviz with movement from web UI
    [robot.xacro]
2016-06-19 Cleaned repo, Hector SLAM not working
    [robot.xacro]
2016-06-19 Move base working with 2D goal
    [robot.xacro]
2016-07-04 Added controller Connected start Mapping as a service to the Web UI button
2016-07-04 Solving Costmap timeout
    [robot.xacro]
2016-07-04 Solved the costmap timeout problem
    first need to run lidar_robot.launch
    then gazebo.launch
    and then at last run move_base.launch
2016-07-04 Added Gazedbo sim in main launch to remove the time inconsistancy problem
    [robot.xacro]
2016-07-05 Removed Accelerometer dependancy Using only Magnetometer in the string
2016-07-06 Moved IMU code to firmware.cpp
2016-07-06 Moved IMU code to firmware.cpp Un Commented create AP and ROSlaunch in serverjs
2016-07-06 Solved issue with RPlidar Frame
2016-07-07 Working Odom Yet to verify,also add the imu_yaw
2016-07-07 Solved the compilation error
    [firmware.cpp]
2016-07-07 Odometry working, but not correctly Need to reset everything with reference frame Need to calibrate TF of IMU to base
2016-07-07 Updated xacro with proper frames
    [robot.xacro]
2016-07-07 IMu rotation not working
    Change the placement of IMU to the center and then remove all the transformations for imu to baselink
    [firmware.cpp]
2016-07-09 Possibly adding the Imu In center

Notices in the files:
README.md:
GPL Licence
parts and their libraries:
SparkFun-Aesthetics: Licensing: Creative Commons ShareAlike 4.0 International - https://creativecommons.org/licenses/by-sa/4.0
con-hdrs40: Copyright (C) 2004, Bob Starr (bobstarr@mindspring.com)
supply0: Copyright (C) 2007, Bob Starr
